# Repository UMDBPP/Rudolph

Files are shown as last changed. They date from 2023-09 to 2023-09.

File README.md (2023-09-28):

# Rudolph
2nd version of a LoRa tracker now using a +30dBm radio coupled with a MIA-M10 for proper tracking.

The system is split into two boards. The primary "logic" board contains the embedded and RF devices. The PowerPack contains all of the necessary circuitry to switch between USB and Battery power sources as well as produce +5V and +3.3V filtered supply rails.

# Bill Of Materials (BOM)
Digi-Key BOM for this project: [https://www.digikey.com/en/mylists/list/V9B8HP1SN9](https://www.digikey.com/en/mylists/list/V9B8HP1SN9)

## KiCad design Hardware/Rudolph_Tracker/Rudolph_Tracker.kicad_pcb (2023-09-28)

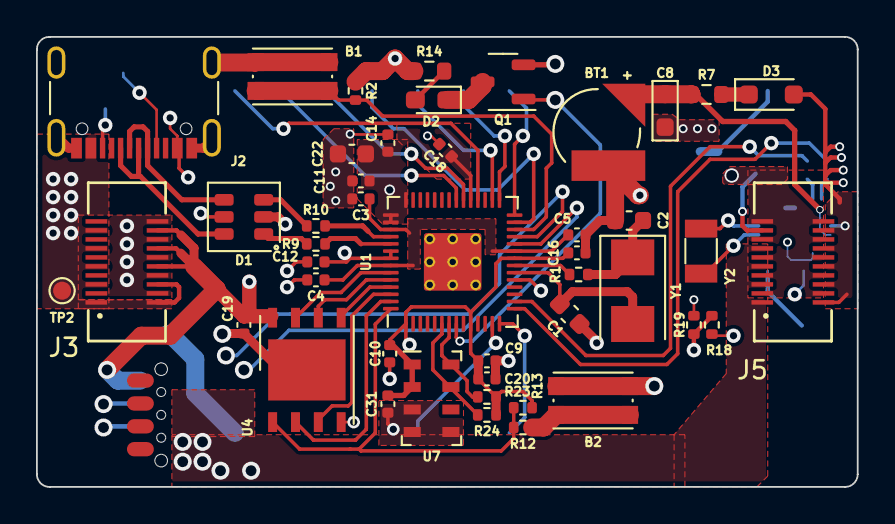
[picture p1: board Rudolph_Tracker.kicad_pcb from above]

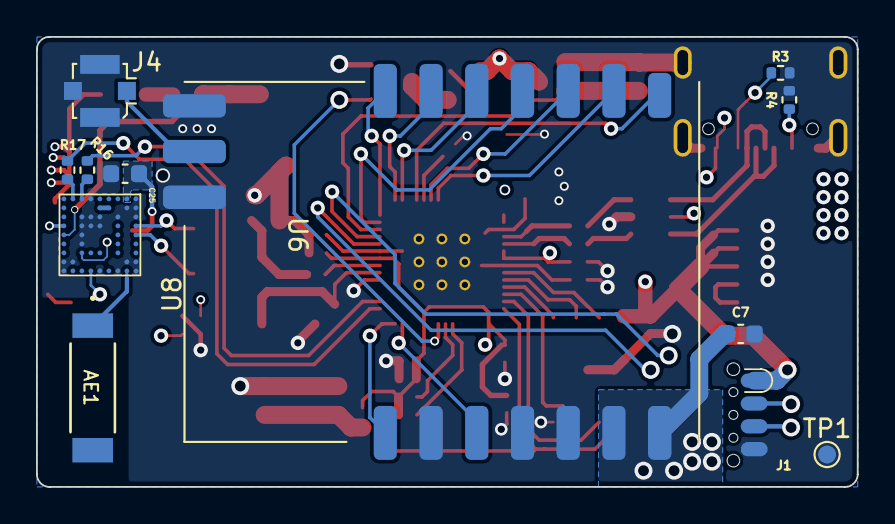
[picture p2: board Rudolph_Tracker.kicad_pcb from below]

Board: 4 copper layers, 45.6 x 25.0 mm, 57 parts (12 on the bottom side), 52 nets.

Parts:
AE1: Antenna; ANT_1575AT_JOT-M
B1, B2: KMR2; SW_Push_1P1T_NO_CK_KMR2
BT1: ML414H IV01E; SEIKO_ML414H_IV01E
C1, C2: 22pF; C_0603_1608Metric
C3, C4, C10, C11, C12, C14, C16, C18, C19, C20, C31: 100nF; C_0402_1005Metric
C5, C9: 1uF; C_0402_1005Metric
C7, C22: 10uF; C_0603_1608Metric
C8: 1uF; R_0603_1608Metric_Pad0.98x0.95mm_HandSolder
C25: 100nF; C_0603_1608Metric
D1: USBLC6-2SC6; SOT-23-6
D2: LED; D_0603_1608Metric_Pad1.05x0.95mm_HandSolder
D3: NSR0530HT1G; D_SOD-323_HandSoldering
J1: SOICbite; SOIC_clipProgSmall
J2: USB_C_Receptacle_USB2.0; USB_C_Receptacle_GCT_USB4105-xx-A_16P_TopMnt_Horizontal
J3, J5: 537480208; CON_537480208
J4: U.FL; U.FL_Molex_MCRF_73412-0110_Vertical
Q1: IRLML0060TRPBF; SOT-23-3
R1, R12: 1k; R_0402_1005Metric
R2, R13, R23, R24: 10k; R_0402_1005Metric
R3, R4: 5.1k; R_0402_1005Metric
R7: 1k; R_0603_1608Metric
R9, R10: 27; R_0402_1005Metric
R14: 590; R_0603_1608Metric
R16, R17: 33; R_0402_1005Metric
R18, R19: 0; R_0402_1005Metric
TP1, TP2: TestPoint; TestPoint_Pad_D1.0mm
U1: RP2040; RP2040-QFN-56
U4: W25Q128JVS; W25Q64JVZP
U6: MIA-M10Q
U7: MS5607-02BA; LGA-8_3x5mm_P1.25mm
U8: DRF1262TL
Y1: 445I23D12M00000; Crystal_SMD_5032-2Pin_5.0x3.2mm
Y2: 32.768k; Crystal_SMD_3215-2Pin_3.2x1.5mm

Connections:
+1V1: C3.1, C4.1, C5.1, U1.23 (DVDD), U1.45 (VREG_VOUT), U1.50 (DVDD)
+3V3: C9.1, C10.1, C11.1, C12.1, C14.1, C16.1, C18.1, C19.1, C20.1, C22.1, C25.1, C31.1, D3.2 (A), J1.1, J3.15, J3.17, J3.19, J5.9, J5.11, J5.13, J5.15, J5.17, J5.19, R2.1, R13.1, R14.1, R23.1, R24.1, U1.1 (IOVDD), U1.10 (IOVDD), U1.22 (IOVDD), U1.33 (IOVDD), U1.42 (IOVDD), U1.43 (ADC_AVDD), U1.44 (VREG_IN), U1.48 (USB_VDD), U1.49 (IOVDD), U4.8 (VCC), U6.B1 (VCC), U6.J4 (V_IO), U7.1 (VDD), U7.2 (PS)
+5V: C7.1, J5.1, J5.3, J5.5, J5.7, U8.6 (VDD), U8.7 (VDD)
/BUSY: U1.35 (GPIO23), U8.9 (BUSY)
/D1: Q1.1 (G), U1.8 (GPIO6)
/DIO1: U1.32 (GPIO21), U8.8 (DIO1)
/GPS_RX: R17.1, U1.15 (GPIO12)
/GPS_TX: R16.1, U1.16 (GPIO13)
/QSPI_SCLK: U1.52 (QSPI_SCLK), U4.6 (CLK)
/QSPI_SD0: U1.53 (QSPI_SD0), U4.5 (DI(IO0))
/QSPI_SD1: U1.55 (QSPI_SD1), U4.2 (DO(IO1))
/QSPI_SD2: U1.54 (QSPI_SD2), U4.3 (IO2)
/QSPI_SD3: U1.51 (QSPI_SD3), U4.7 (IO3)
/QSPI_SS: R12.2, R13.2, U1.56 (QSPI_SS), U4.1 (~CS)
/SCL: R23.2, U1.7 (GPIO5), U7.8 (SCLK)
/SDA: R24.2, U1.6 (GPIO4), U7.7 (SDI/SDA)
/SPI0_CS: U1.28 (GPIO17), U8.14 (NSS)
/SPI0_MISO: U1.27 (GPIO16), U8.11 (MISO)
/SPI0_MOSI: U1.30 (GPIO19), U8.12 (MOSI)
/SPI0_SCK: U1.29 (GPIO18), U8.13 (SCK)
/SW: U1.14 (GPIO11), U8.1 (SW)
/SWCLK: J1.3, U1.24 (SWCLK)
/SWD: J1.2, U1.25 (SWD)
/TXEN: U1.13 (GPIO10), U8.3 (TXEN)
/USB_D+: D1.1 (L1), R9.2
/USB_D-: D1.3 (L2), R10.2
/V_BCKP: BT1.1 (+), C8.1, R7.2, U6.J5 (V_BCKP)
/~RST: U1.34 (GPIO22), U8.10 (RST)
GND: B1.1, B2.1, BT1.2 (-), C1.1, C2.1, C3.2, C4.2, C5.2, C7.2, C8.2, C9.2, C10.2, C11.2, C12.2, C14.2, C16.2, C18.2, C19.2, C20.2, C22.2, C25.2, C31.2, D1.2 (VN), J1.4, J2.A1 (GND), J2.A12 (GND), J2.B1 (GND), J2.B12 (GND), J2.S1 (SHIELD), J3.2, J3.4, J3.6, J3.8, J3.10, J3.12, J3.14, J3.16, J3.18, J3.20, J4.2 (Ext), J5.2, J5.4, J5.6, J5.8, J5.10, J5.12, J5.14, J5.16, J5.18, J5.20, Q1.2 (S), R3.2, R4.2, R18.2, R19.2, TP1.1, U1.19 (TESTEN), U1.57 (GND), U4.4 (GND), U4.9 (EP), U6.A1 (GND), U6.A2 (GND), U6.A3 (GND), U6.A8 (GND), U6.A9 (GND), U6.B2 (GND), U6.B8 (GND), U6.C3 (GND), U6.C9 (GND), U6.E3 (GND), U6.E4 (GND), U6.E9 (GND), U6.F1 (GND), U6.F3 (GND), U6.F4 (GND), U6.G3 (GND), U6.G4 (GND), U6.G5 (GND), U6.G6 (GND), U6.H8 (GND), U6.J8 (GND), U6.J9 (GND), U7.3 (GND), U7.4 (CSB), U7.5 (CSB), U8.2 (GND), U8.4 (GND), U8.5 (GND), U8.15 (GND), U8.17 (GND)
unnamed: AE1.1 (A), U6.B9 (RF_IN)
unnamed: B2.2, R12.1
unnamed: C2.2, R1.1, Y1.1
unnamed: D1.6 (L1), J2.A6 (D+), J2.B6 (D+)
unnamed: D1.4 (L2), J2.A7 (D-), J2.B7 (D-)
unnamed: D2.2 (A), R14.2
unnamed: D2.1 (K), Q1.3 (D)
unnamed: D3.1 (K), R7.1
unnamed: J2.A5 (CC1), R3.1
unnamed: J2.B5 (CC2), R4.1
unnamed: J4.1 (In), U8.16 (ANT)
unnamed: R18.1, U6.F9 (RSRVD)
unnamed: R19.1, U6.G7 (RSRVD)
unnamed: B1.2, R2.2, U1.26 (RUN)
unnamed: R10.1, U1.46 (USB_DM)
unnamed: R9.1, U1.47 (USB_DP)
unnamed: C1.2, U1.20 (XIN), Y1.2
unnamed: R1.2, U1.21 (XOUT)
unnamed: U6.A4 (RTC_I), Y2.2
unnamed: U6.A5 (RTC_O), Y2.1
unnamed: R17.2, U6.H1 (RX)
unnamed: R16.2, U6.G1 (TX)
VBUS: D1.5 (VP), J2.A4 (VBUS), J2.A9 (VBUS), J2.B4 (VBUS), J2.B9 (VBUS), J3.1, J3.3, J3.5, J3.7, J3.9, J3.11, J3.13, TP2.1

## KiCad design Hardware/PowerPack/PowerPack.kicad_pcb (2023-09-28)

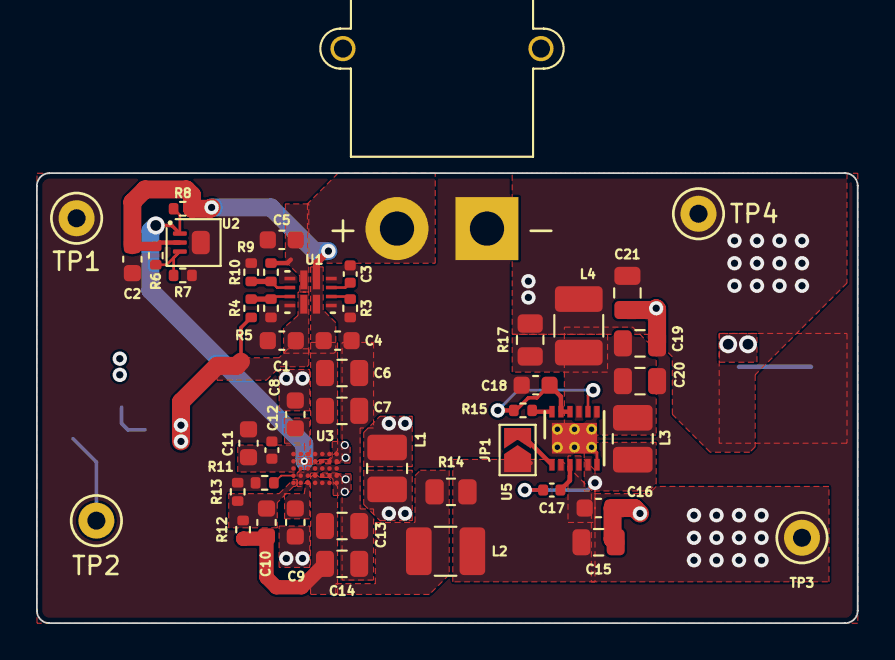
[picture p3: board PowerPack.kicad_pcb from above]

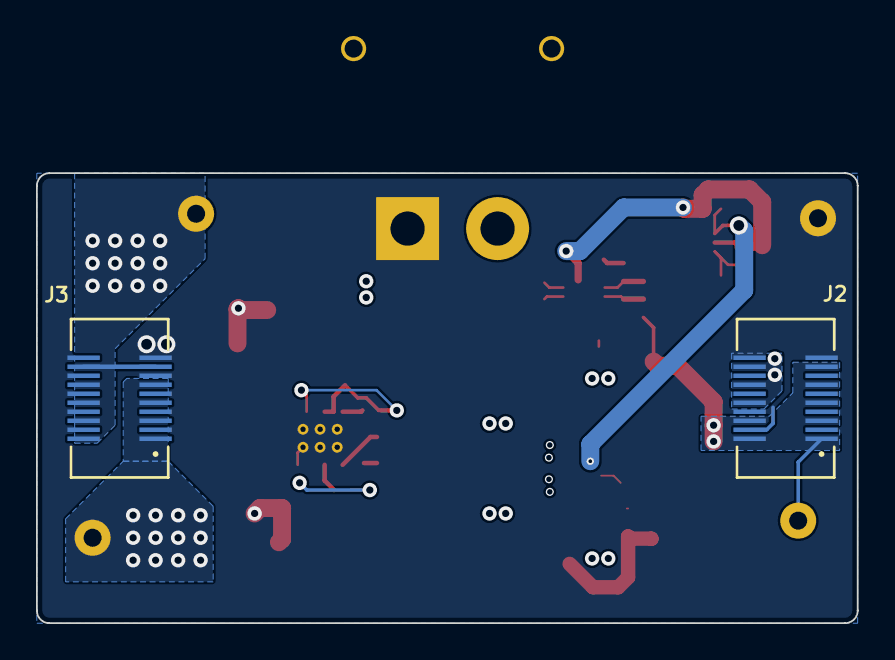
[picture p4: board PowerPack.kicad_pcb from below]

Board: 4 copper layers, 45.6 x 25.0 mm, 51 parts (2 on the bottom side), 26 nets.

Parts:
C1, C5: 10uF; C_0603_1608Metric
C2, C4, C18: 1uF; C_0603_1608Metric
C3: 10nF; C_0402_1005Metric
C6, C7, C13, C14: 10uF; C_0805_2012Metric
C8, C9: 220nF; C_0603_1608Metric
C10: 10pF; C_0603_1608Metric
C11: 2.2uF; C_0603_1608Metric
C12: 470nF; C_0402_1005Metric
C15, C19, C20, C21: 15uF; C_0805_2012Metric
C16: 4.7uF; C_0603_1608Metric
C17: 0.1uF; C_0402_1005Metric
J2, J3: 529910208; CON_529910208
J4: XT30; AMASS_XT30PW-M_1x02_P2.50mm_Horizontal
JP1: SolderJumper_2_Open; SolderJumper-2_P1.3mm_Open_TrianglePad1.0x1.5mm
L1: 1.0uH; L_1008_2520Metric_Pad1.43x2.20mm_HandSolder
L2, L4: 3.3uH; L_1210_3225Metric_Pad1.42x2.65mm_HandSolder
L3: 2.2uH; L_1008_2520Metric_Pad1.43x2.20mm_HandSolder
R3: 44.2k; R_0402_1005Metric
R4, R9: 23.7k; R_0402_1005Metric
R5, R10: 5k; R_0402_1005Metric
R6: 1.05M; R_0402_1005Metric
R7: 154k; R_0402_1005Metric
R8: 510k; R_0402_1005Metric
R11: 64.9k; R_0402_1005Metric
R12: 178k; R_0402_1005Metric
R13: 12.7k; R_0402_1005Metric
R14, R17: 100m; R_0805_2012Metric
R15: 20k; R_0402_1005Metric
TP1, TP2, TP3, TP4: TestPoint; TestPoint_Keystone_5000-5004_Miniature
U1: TPS2121RUXR; TPS2121
U2: LT6703CDC-3; DFN-3-1EP-2x2mm_P0.5mm_EP1x1.35mm
U3: MAX77857; MAX77857-35WLP
U5: MAX25232ATCB/V+T; MAX25232

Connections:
+3V3: C21.1, J2.15, J2.17, J2.19, J3.9, J3.11, J3.13, J3.15, J3.17, J3.19, L4.2, R17.2, TP4.1
+5V: C15.1, C16.1, J3.1, J3.3, J3.5, J3.7, JP1.1 (A), L2.2, R14.2, TP3.1, U5.2 (EN), U5.4 (SUP)
+BATT: C5.1, J4.2, R9.1, U1.2 (IN2)
+VDC: C2.1, C4.1, C6.1, C7.1, R6.1, R8.1, U1.1 (OUT), U1.8 (OUT), U2.2 (V+), U3.A4 (IN), U3.A5 (IN), U3.A6 (IN), U3.B4 (IN)
/LVC: R8.2, U2.1 (OUT), U3.B2 (EN), U3.B3 (EN)
GND: C1.2, C2.2, C3.2, C4.2, C5.2, C6.2, C7.2, C11.2, C12.2, C13.2, C14.2, C15.2, C16.2, C18.2, C19.2, C20.2, C21.2, J2.2, J2.4, J2.6, J2.8, J2.10, J2.12, J2.14, J2.16, J2.18, J2.20, J3.2, J3.4, J3.6, J3.8, J3.10, J3.12, J3.14, J3.16, J3.18, J3.20, J4.1, R3.2, R5.2, R7.2, R10.2, R11.1, R13.2, TP1.1, U1.3 (CP2), U1.6 (PR1), U1.9 (ST), U1.12 (GND), U2.4 (V-), U3.C3 (PGND), U3.C4 (PGND), U3.C5 (PGND), U3.C6 (PGND), U3.C7 (PGND), U3.D2 (PGND), U3.D3 (PGND), U3.E2 (AGND), U5.6 (PGND), U5.7 (AGND), U5.EP (GND)
unnamed: C8.2, L1.1, U3.A7 (LX1), U3.B5 (LX1), U3.B6 (LX1), U3.B7 (LX1)
unnamed: C9.1, L1.2, U3.D5 (LX2), U3.D6 (LX2), U3.D7 (LX2), U3.E7 (LX2)
unnamed: C10.1, C13.1, C14.1, L2.1, R12.1, R14.1, U3.D4 (OUT), U3.E4 (OUT), U3.E5 (OUT), U3.E6 (OUT)
unnamed: JP1.2 (B), U5.1 (SPS)
unnamed: R3.1, U1.10 (ILM)
unnamed: R4.2, R5.1, U1.5 (OV1)
unnamed: R9.2, R10.1, U1.4 (OV2)
unnamed: C3.1, U1.11 (SS)
unnamed: R6.2, R7.1, U2.3 (IN+)
unnamed: C8.1, U3.A3 (BST1)
unnamed: C9.2, U3.E3 (BST2)
unnamed: C10.2, R12.2, R13.1, U3.E1 (FB)
unnamed: C11.1, C12.1, U3.A1 (SCL), U3.A2 (VIO), U3.B1 (SDA), U3.C1 (VL)
unnamed: R11.2, U3.D1 (SEL)
unnamed: C18.1, R15.2, U5.8 (FB), U5.10 (BIAS), U5.11 (SYNC)
unnamed: C17.1, U5.3 (BST)
unnamed: C17.2, L3.1, U5.5 (LX)
unnamed: C19.1, C20.1, L3.2, L4.1, R17.1, U5.9 (OUT)
unnamed: R15.1, U5.12 (PGOOD)
VBUS: C1.1, J2.1, J2.3, J2.5, J2.7, J2.9, J2.11, J2.13, R4.1, TP2.1, U1.7 (IN1)

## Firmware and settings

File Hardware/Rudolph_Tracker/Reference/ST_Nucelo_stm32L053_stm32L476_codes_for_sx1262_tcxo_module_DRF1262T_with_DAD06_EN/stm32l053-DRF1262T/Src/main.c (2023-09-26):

/*
******************************************************
	*Soft VERSION:1.1
	*Company:DORJI
	*Email: sales@dorji.com
	*Web: 	http://www.dorji.com
*****************************************************
*/
#include "main.h"
#include "stm32l0xx_hal.h"
#include "spi.h"
#include "tim.h"
#include "usart.h"
#include "gpio.h"

/* USER CODE BEGIN Includes */
#include "stdio.h"
#include "string.h"
#include "sx126x-board.h"
#include "radio.h"
#include "switch.h"
/* USER CODE END Includes */


/* USER CODE BEGIN PV */
 SWITCH_STATE_ST user_select_mode = {0};   //user selected mode
/* USER CODE END PV */

void SystemClock_Config(void);

/* USER CODE BEGIN PFP */

/* USER CODE END PFP */

/* USER CODE BEGIN 0 */
#define Get_NIRQ()  HAL_GPIO_ReadPin(RADIO_DIO0_GPIO_Port,RADIO_DIO0_Pin)

/*
  Notes:
  1)The jumper T/R on DRF1262G is connected to SWCLK£¨PA14) so this jumper must be unconnected in order to download the codes into ST-NUCLEO board successfuly.
  2)If no jumpers are connected, the default settings will be: freq=868Mhz,mode=TX,power=22,BW=250kHZ,SF=12
    The freqeuncy selection for USE_BAND_868 and USE_BAND_915 can be done in KEIL MDK5: Options for targets->c/c++->Define global variable
  
   SF1   SF2  SF3       Spreading Factor    Switch Val
	 OFF   OFF  OFF             12          			0
	 ON    OFF  OFF             11								1
	 OFF   ON   OFF             10								2
	 OFF   OFF  ON               9								4
	 ON 	 ON   OFF              8          			3
	 ON    OFF  ON 							 7          			5
	 OFF   ON   ON               6          			6
   ON    ON   ON               5          			7
	 


   SB1   SB2   SB3   SB4        Bandwidth 		Switch Val
   OFF   OFF   OFF   OFF         250KHz           0
   ON    OFF   OFF   OFF         125KHz           1
   OFF   ON    OFF   OFF         60.5KHz          2
   OFF   OFF   ON    OFF         41.67KHz         4
   OFF   OFF   OFF   ON          31.25KHz         8
   ON    ON    OFF   OFF         20.83KHz         3
   ON    OFF   ON    OFF         16.63KHz         5
   ON    OFF   OFF   ON          10.42KHz         9
   OFF   ON    ON    OFF         7.81KHz          6
   others                        500KHz
 */
 #if defined( USE_BAND_868 )

#define RF_FREQUENCY                                868000000 // Hz

#elif defined( USE_BAND_915 )

#define RF_FREQUENCY                                915000000 // Hz

#else
    #error "Please define a frequency band in the compiler options."
#endif

#define TX_OUTPUT_POWER                             22        // dBm TX output power

#if defined( USE_MODEM_LORA )

#define LORA_BANDWIDTH                              1         // Bandwidth: 125khz,lookfor radio.c line 392 
																															//[250kHZ,125khz,62.5khz,20.83kHZ,41.67KHZ
																															//16.63kHZ,7.81KHZ,500khz,31.25KHZ,10.42kHZ]
#define LORA_SPREADING_FACTOR                       11         // Spreading Factor: SF11 [SF5..SF12]
#define LORA_CODINGRATE                             1         // [1: 4/5,
                                                              //  2: 4/6,
                                                              //  3: 4/7,
                                                              //  4: 4/8]
#define LORA_PREAMBLE_LENGTH                        8         // Same for Tx and Rx
#define LORA_SYMBOL_TIMEOUT                         0         // Symbols
#define LORA_FIX_LENGTH_PAYLOAD_ON                  false
#define LORA_IQ_INVERSION_ON                        false

#elif defined( USE_MODEM_FSK )

#define FSK_FDEV                                    25e3      // Hz 
#define FSK_DATARATE                                50e3      // bps
#define FSK_BANDWIDTH                               100e3     // Hz >> DSB in sx126x
#define FSK_AFC_BANDWIDTH                           100e3     // Hz
#define FSK_PREAMBLE_LENGTH                         5         // Same for Tx and Rx
#define FSK_FIX_LENGTH_PAYLOAD_ON                   false

#else
    #error "Please define a modem in the compiler options."
#endif

typedef enum
{
    LOWPOWER,
    RX,
    RX_TIMEOUT,
    RX_ERROR,
    TX,
    TX_TIMEOUT,
}States_t;

#define RX_TIMEOUT_VALUE                            1000
#define BUFFER_SIZE                                 64 // Define the payload size here

const uint8_t PingMsg[] = "PING";

uint16_t BufferSize = BUFFER_SIZE;
uint8_t Buffer[BUFFER_SIZE];

States_t State = LOWPOWER;

int8_t RssiValue = 0;
int8_t SnrValue = 0;

/*!
 * Radio events function pointer
 */
static RadioEvents_t RadioEvents;

/*!
 * \brief Function to be executed on Radio Tx Done event
 */
void OnTxDone( void );

/*!
 * \brief Function to be executed on Radio Rx Done event
 */
void OnRxDone( uint8_t *payload, uint16_t size, int16_t rssi, int8_t snr );

/*!
 * \brief Function executed on Radio Tx Timeout event
 */
void OnTxTimeout( void );

/*!
 * \brief Function executed on Radio Rx Timeout event
 */
void OnRxTimeout( void );

/*!
 * \brief Function executed on Radio Rx Error event
 */
void OnRxError( void );
/* USER CODE END 0 */

/**
  * @brief  The application entry point.
  *
  * @retval None
  */
int main(void)
{
  /* USER CODE BEGIN 1 */
		uint8_t i = 0;
  /* USER CODE END 1 */

  /* MCU Configuration----------------------------------------------------------*/

  /* Reset of all peripherals, Initializes the Flash interface and the Systick. */
  HAL_Init();

  /* Configure the system clock */
  SystemClock_Config();

  /* Initialize all configured peripherals */
  MX_GPIO_Init();
  MX_SPI1_Init();
  MX_TIM2_Init();
  MX_USART1_UART_Init();
  /* USER CODE BEGIN 2 */
  printf("Device is init OK...\r\n");
  HAL_TIM_Base_Start_IT(&htim2);
	
	user_select_mode = Check_switch();  //obtain users' selection
				 
	// Radio initialization
    RadioEvents.TxDone = OnTxDone;
    RadioEvents.RxDone = OnRxDone;
    RadioEvents.TxTimeout = OnTxTimeout;
    RadioEvents.RxTimeout = OnRxTimeout;
    RadioEvents.RxError = OnRxError;

    Radio.Init( &RadioEvents );

    Radio.SetChannel( RF_FREQUENCY );

#if defined( USE_MODEM_LORA )

    Radio.SetTxConfig( MODEM_LORA, TX_OUTPUT_POWER, 0, user_select_mode.band_width,
                                   user_select_mode.spread_factor, LORA_CODINGRATE,
                                   LORA_PREAMBLE_LENGTH, LORA_FIX_LENGTH_PAYLOAD_ON,
                                   true, 0, 0, LORA_IQ_INVERSION_ON, 3000 );

    Radio.SetRxConfig( MODEM_LORA, user_select_mode.band_width, user_select_mode.spread_factor,
                                   LORA_CODINGRATE, 0, LORA_PREAMBLE_LENGTH,
                                   LORA_SYMBOL_TIMEOUT, LORA_FIX_LENGTH_PAYLOAD_ON,
                                   0, true, 0, 0, LORA_IQ_INVERSION_ON, true );

#elif defined( USE_MODEM_FSK )

    Radio.SetTxConfig( MODEM_FSK, TX_OUTPUT_POWER, FSK_FDEV, 0,
                                  FSK_DATARATE, 0,
                                  FSK_PREAMBLE_LENGTH, FSK_FIX_LENGTH_PAYLOAD_ON,
                                  true, 0, 0, 0, 3000 );

    Radio.SetRxConfig( MODEM_FSK, FSK_BANDWIDTH, FSK_DATARATE,
                                  0, FSK_AFC_BANDWIDTH, FSK_PREAMBLE_LENGTH,
                                  0, FSK_FIX_LENGTH_PAYLOAD_ON, 0, true,
                                  0, 0,false, true );

#else
    #error "Please define a frequency band in the compiler options."
#endif
	 if(RX_MODE == user_select_mode.tx_rx_mode)
	{
			Radio.Rx(0);
	}else
	{
		Radio.Send((uint8_t*)Buffer, 4 );
	}
  /* USER CODE END 2 */

  /* Infinite loop */
  /* USER CODE BEGIN WHILE */
  while (1)
  {

  /* USER CODE END WHILE */

  /* USER CODE BEGIN 3 */
	if(RX_MODE == user_select_mode.tx_rx_mode)
		{
		        if(  RX == State )  //Judge if the data is received
        { 
					HAL_GPIO_TogglePin(LED_BLUE_LEFT_GPIO_Port,LED_BLUE_LEFT_Pin);
          HAL_UART_Transmit(&huart1, (uint8_t *)Buffer, BufferSize, 0xFFFF);
					printf("\r\n");
					printf("RssiValue:%d,SnrValue:%d,State:%d\r\n",RssiValue,SnrValue,State);					
          State = LOWPOWER;

        }
		}else if (TX == State) //Judge if data transmission is finished
		{  
			  i++;  //unsigned char
			  sprintf((char*)Buffer,"%s%03d",PingMsg,i);
        Radio.Send((uint8_t*)Buffer, 7 );
			  HAL_GPIO_TogglePin(LED_RED_LEFT_GPIO_Port,LED_RED_LEFT_Pin);
				DelayMs(500);
		}
        // Process Radio IRQ
        Radio.IrqProcess( );				
  }
  /* USER CODE END 3 */

}

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
/* USER CODE BEGIN 4 */
void OnTxDone( void )
{
//    Radio.Sleep( );
    State = TX;
}

void OnRxDone( uint8_t *payload, uint16_t size, int16_t rssi, int8_t snr )
{
//    Radio.Sleep( );
    BufferSize = size;
    memcpy( Buffer, payload, BufferSize );
    RssiValue = rssi;
    SnrValue = snr;
    State = RX;
}

void OnTxTimeout( void )
{
 //   Radio.Sleep( );
    State = TX_TIMEOUT;
}

void OnRxTimeout( void )
{
//    Radio.Sleep( );
    State = RX_TIMEOUT;
}

void OnRxError( void )
{
//    Radio.Sleep( );
    State = RX_ERROR;
}
/* USER CODE END 4 */
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


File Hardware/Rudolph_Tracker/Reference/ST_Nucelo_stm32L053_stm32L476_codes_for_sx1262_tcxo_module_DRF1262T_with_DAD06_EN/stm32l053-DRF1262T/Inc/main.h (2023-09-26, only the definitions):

#define RADIO_RESET_Pin GPIO_PIN_0
#define RADIO_RESET_GPIO_Port GPIOA
#define LED_BLUE_LEFT_Pin GPIO_PIN_1
#define LED_BLUE_LEFT_GPIO_Port GPIOA
#define LED_RED_LEFT_Pin GPIO_PIN_4
#define LED_RED_LEFT_GPIO_Port GPIOA
#define DORJI_SB1_Pin GPIO_PIN_4
#define DORJI_SB1_GPIO_Port GPIOC
#define DORJI_SB2_Pin GPIO_PIN_5
#define DORJI_SB2_GPIO_Port GPIOC
#define LED_BLUE_RIGHT_Pin GPIO_PIN_12
#define LED_BLUE_RIGHT_GPIO_Port GPIOB
#define DORI_SB3_Pin GPIO_PIN_6
#define DORI_SB3_GPIO_Port GPIOC
#define DORJI_SB4_Pin GPIO_PIN_8
#define DORJI_SB4_GPIO_Port GPIOC
#define RADIO_NSS_Pin GPIO_PIN_8
#define RADIO_NSS_GPIO_Port GPIOA
#define DORJI_L_F_Pin GPIO_PIN_11
#define DORJI_L_F_GPIO_Port GPIOA
#define DORJI_T_R_Pin GPIO_PIN_14
#define DORJI_T_R_GPIO_Port GPIOA
#define DORJI_SF1_Pin GPIO_PIN_10
#define DORJI_SF1_GPIO_Port GPIOC
#define DORJI_SF2_Pin GPIO_PIN_11
#define DORJI_SF2_GPIO_Port GPIOC
#define DORJI_SF3_Pin GPIO_PIN_12
#define DORJI_SF3_GPIO_Port GPIOC
#define RADIO_BUSY_Pin GPIO_PIN_3
#define RADIO_BUSY_GPIO_Port GPIOB
#define RADIO_DIO0_Pin GPIO_PIN_4
#define RADIO_DIO0_GPIO_Port GPIOB
#define RADIO_DIO0_EXTI_IRQn EXTI4_15_IRQn
#define LED_RED_RIGHT_Pin GPIO_PIN_7
#define LED_RED_RIGHT_GPIO_Port GPIOB

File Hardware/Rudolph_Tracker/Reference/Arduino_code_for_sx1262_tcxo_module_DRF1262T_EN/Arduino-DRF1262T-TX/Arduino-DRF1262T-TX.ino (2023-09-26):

#include <avr/io.h>
#include <avr/interrupt.h>
#include <SPI.h>
#include "radio.h"
#include "timer1.h"
#include "sx126x.h"
#include "sx126x-board.h"
#define Get_NIRQ()       digitalRead(Dio1Pin)
/*
 * if you want to use TCXO please open sx1262.h line 29
*/

uint8_t mode = USER_MODE_TX;   /*mode  SET current work mode: TX or RX*/
/*Default frequency：868MHZ Bandwidth：125KHZ，RF_FACTOR：11 */
#define RF_FREQUENCY                                868000000 // Hz  center frequency
#define TX_OUTPUT_POWER                             22        // dBm tx output power
#define LORA_BANDWIDTH                              1         // bandwidth=125khz   0:250kHZ,1:125kHZ,2:62kHZ,3:20kHZ.... lookfor radio line 392                                                               
#define LORA_SPREADING_FACTOR                       11        // spreading factor=11 [SF5..SF12]
#define LORA_CODINGRATE                             1         // [1: 4/5,
                                                              //  2: 4/6,
                                                              //  3: 4/7,
                                                              //  4: 4/8]
#define LORA_PREAMBLE_LENGTH                        8         // Same for Tx and Rx
#define LORA_SYMBOL_TIMEOUT                         0         // Symbols
#define LORA_FIX_LENGTH_PAYLOAD_ON                  false     // variable data payload
#define LORA_IQ_INVERSION_ON                        false

typedef enum
{
    LOWPOWER,
    RX,
    RX_TIMEOUT,
    RX_ERROR,
    TX,
    TX_TIMEOUT,
}States_t;

#define RX_TIMEOUT_VALUE                            1000
#define BUFFER_SIZE                                 64 // Define the payload size here
States_t State = LOWPOWER;

RadioEvents_t RadioEvents;
uint16_t BufferSize = BUFFER_SIZE;
uint8_t  Buffer[BUFFER_SIZE];
int8_t RssiValue = 0;
int8_t SnrValue  = 0;

void OnTxDone( void );
void OnRxDone( uint8_t *payload, uint16_t size, int16_t rssi, int8_t snr );
void OnTxTimeout( void );
void OnRxTimeout( void );
void OnRxError( void );

uint8_t i = 0;

void setup()
{
    timer1_init();
    SPI.beginTransaction(SPISettings(2000000, MSBFIRST, SPI_MODE0));
    Serial.begin(9600);           //set baud rate
    SX126xIoInit();               //Initializes the radio I/Os pins
    SPI.begin();

    pinMode (Led1BluePin, OUTPUT);
    pinMode (Led1RedPin, OUTPUT);
    digitalWrite(Led1BluePin,1);
    digitalWrite(Led1RedPin,1);

    // Radio initialization
    RadioEvents.TxDone = OnTxDone;
    RadioEvents.RxDone = OnRxDone;
    RadioEvents.TxTimeout = OnTxTimeout;
    RadioEvents.RxTimeout = OnRxTimeout;
    RadioEvents.RxError = OnRxError;

    Radio.Init( &RadioEvents );
    Radio.SetChannel( RF_FREQUENCY );
    
    Radio.SetTxConfig( MODEM_LORA, TX_OUTPUT_POWER, 0,LORA_BANDWIDTH,
                                   LORA_SPREADING_FACTOR, LORA_CODINGRATE,
                                   LORA_PREAMBLE_LENGTH, LORA_FIX_LENGTH_PAYLOAD_ON,
                                   true, 0, 0, LORA_IQ_INVERSION_ON, 3000 );

    Radio.SetRxConfig( MODEM_LORA, LORA_BANDWIDTH,LORA_SPREADING_FACTOR,
                                   LORA_CODINGRATE, 0, LORA_PREAMBLE_LENGTH,
                                   LORA_SYMBOL_TIMEOUT, LORA_FIX_LENGTH_PAYLOAD_ON,
                                   0, true, 0, 0, LORA_IQ_INVERSION_ON, true );
                                   
  if(USER_MODE_RX == mode)
    {
      
     Radio.Rx(0); 
     digitalWrite(Led1BluePin,0);
     Serial.println("Now is RX"); 
    }else
    {
    Radio.Send((uint8_t*)&i, 1 );                                 
    }
}

void loop() 
{
  // put your main code here, to run repeatedly:
  if(USER_MODE_RX == mode)
    {
            if(  0 != State )
        { 
          Serial.println(Buffer[0],DEC);  //print received characters 
          
          digitalWrite(Led1BluePin,digitalRead(Led1BluePin)^1);               
          State = LOWPOWER;

        }
    }else if(TX == State)
    {  
        delay(500);
        i++;
        Radio.Send((uint8_t*)&i, 1 );  //send one testing character, users can change the content   
        digitalWrite(Led1RedPin,digitalRead(Led1RedPin)^1);  
    }
        // Process Radio IRQ
     if(Get_NIRQ())
     {
        Radio.IrqProcess( );         
     }  

  }
 



void OnTxDone( void )
{
//    Radio.Sleep( );
    State = TX;
}

void OnRxDone( uint8_t *payload, uint16_t size, int16_t rssi, int8_t snr )
{
//    Radio.Sleep( );
    BufferSize = size;
    memcpy( Buffer, payload, BufferSize );
    RssiValue = rssi;
    SnrValue = snr;
    State = RX;
}

void OnTxTimeout( void )
{
   //   Radio.Sleep( );
      State = TX_TIMEOUT;
}

void OnRxTimeout( void )
{
  //    Radio.Sleep( );
      State = RX_TIMEOUT;
}

void OnRxError( void )
{
  //    Radio.Sleep( );
      State = RX_ERROR;
}

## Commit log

2023-09-26 init with first routing pass
    [Pick Place for SX1276RF1KAS_e269v01a.xlsx, PowerPack.kicad_pcb, PowerPack.kicad_sch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]
2023-09-26 flipped some connectors
    [PowerPack.kicad_pcb, Rudolph_Tracker.kicad_pcb]
2023-09-26 generating gerbers
    [PowerPack-B_Cu.gbl, PowerPack-B_Mask.gbs, PowerPack-B_Paste.gbp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]
2023-09-28 generating some BOMs
    [PowerPack-B_Cu.gbl, PowerPack-B_Mask.gbs, PowerPack-B_Paste.gbp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]
2023-11-03 messing with libraries
    [PowerPack.kicad_sch, Rudolph_Tracker.kicad_sch]

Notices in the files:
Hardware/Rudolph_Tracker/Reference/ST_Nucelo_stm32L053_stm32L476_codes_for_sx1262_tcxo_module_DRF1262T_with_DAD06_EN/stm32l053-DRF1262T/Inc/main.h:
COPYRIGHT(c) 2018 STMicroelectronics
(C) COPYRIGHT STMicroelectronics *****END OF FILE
